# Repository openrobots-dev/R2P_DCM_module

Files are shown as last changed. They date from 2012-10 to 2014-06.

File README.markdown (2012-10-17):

MOTORBOARD MODULE
-----------------

This is a motor controller board that features an high power 24V, 20A H-bridge, current sense and quadrature encoder interface.
The MotorBoard module is supposed to work together with other smart modules, publishing data on CAN bus using a publish/subscriber QoS enabled middleware (under development).
The overall system should provide the devices and functionalities commonly used in robot prototyping, speeding up the development process and reducing the engineering time, leaving more time to research activities. The system is also supposed to enable students and amateurs to easily build robots without advanced hardware knowledge.

### Hardware

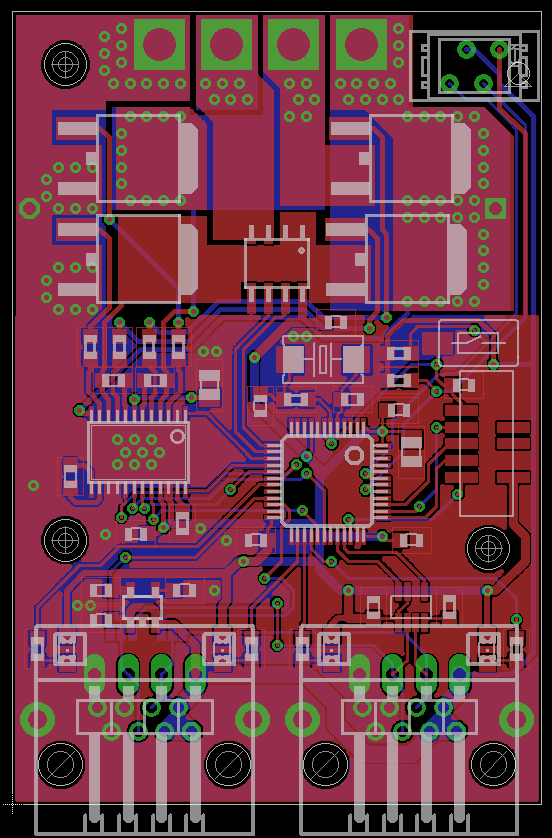
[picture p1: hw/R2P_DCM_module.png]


The MotorBoard module is run by a STM32 ARM Cortex-M3 microcontroller that generates driving signals for the H-Bridge, monitors the current drawn by the motor and reads the incremental encoder feedback.
The microcontroller also runs a PID controller that can follow a position, speed or current (torque) set-point received on a specific topic over the CAN bus network.

The power stage of the MotorBoard features:

- ST STD120N4F6 N-channel 40 V, 3.5 mOhm, 80A power MOSFETs
- Allegro A4941 MOSFET driver
- Allegro ACS711 Hall-effect current sensor

Modules are connected together by a single cable, that transports CAN signals and 5V power. Each module has two ports, enabling chain connections.

A double connector footprint (RJ45 + pin header) is provided, so the user can choose which cabling fits better his needs:

- RJ45 has been chosen as it provides shielded twisted wires for 1Mbit CAN networking in harsh environments and cables are easy to find.
- pin header has been chosen to also give a space saving and simple connection when modules are close and RJ45 jack/plug pairing space is a problem. This header also enables using the IMU module outside our framework, accessing it through a simple TTL UART interface.

The four status LEDs are placed under RJ45 plug light pipes entrance, so it is only needed to solder the preferred connector without any other layout changes.

The left connector has the option to expose the TTL UART interface, instead of the CAN bus interface, by a solder jumper placed on the bottom of the board.

### Firmware

A demo firmware which tests the various hardware components is available.
The full firmware featuring closed loop control is under development.

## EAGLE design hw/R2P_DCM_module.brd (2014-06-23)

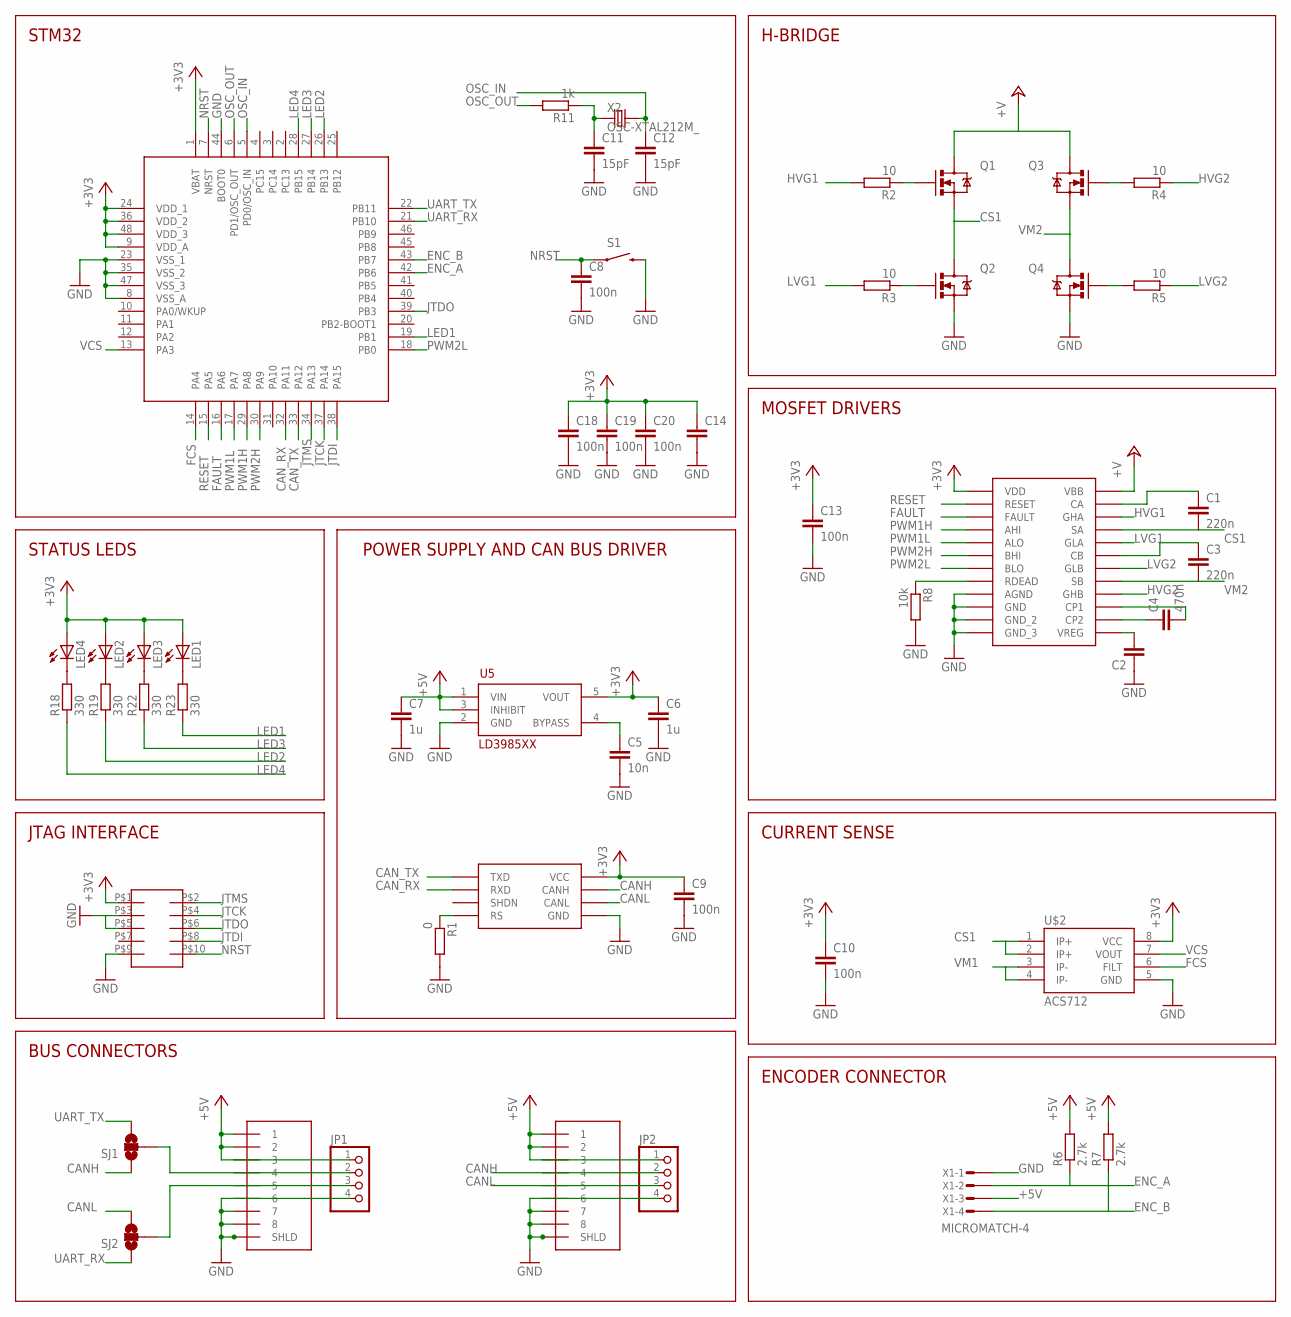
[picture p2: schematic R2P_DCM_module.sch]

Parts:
1, 2: RJ45-43860; 0438600010
C1, C3: 220n; C0603
C2, C14: C-EUC0805; C0805
C4: 470n; C0603
C5: 10n; C0603
C6, C7: 1u; C0603
C8, C9, C10, C13, C18, C19, C20: 100n; C0603
C11, C12: 15pF; C0603
JP1, JP2: PINHD-1X4/90; 1X04/90
LED1, LED2, LED3, LED4: LEDCHIPLED_0805; CHIPLED_0805
Q1, Q2, Q3, Q4: MOSFET-NCHANNELFDD8580; DPAK
R1: 0; R0603
R2, R3, R4, R5: 10; R0603
R6, R7: 2.7k; R0603
R8: 10k; R0603
R11: 1k; R0603
R18, R19, R22, R23: 330; R0603
S1: SWITCH-MOMENTARY-2-SMD-1101NE; TACTILE-SWITCH-1101NE
SJ1, SJ2: SOLDERJUMPER_2WAYPASTE1&2; SJ_3_PASTE1&2
SOT1: MAX3051; SOT23-8L
U1: STM32F103CX; LQFP48
U5: LD3985XX; SOT23-5L
U$1: A4940; TSSOP24
U$2: ACS712; SO08
U$4: FTSH-105
X1: MICROMATCH-4
X2: OSC-XTAL212M_; 4X6

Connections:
+3V3: C6.1, C9.1, C10.1, C13.1, C14.1, C18.1, C19.1, C20.1, LED1.A, LED2.A, LED3.A, LED4.A, SOT1.P$3 (VCC), U1.1 (VBAT), U1.9 (VDD_A), U1.24 (VDD_1), U1.36 (VDD_2), U1.48 (VDD_3), U5.5 (VOUT), U$1.21 (VDD), U$2.8 (VCC), U$4.P$1
+5V: 1.P$1 (1), 1.P$2 (2), 1.P$3 (3), 2.P$1 (1), 2.P$2 (2), 2.P$3 (3), C7.1, JP1.1, JP2.1, R6.2, R7.2, U5.1 (VIN), U5.3 (INHIBIT), X1.3
+V: Q1.4 (D), Q3.4 (D), U$1.12 (VBB)
CANH: 2.P$4 (4), JP2.2, SJ1.1, SOT1.P$7 (CANH)
CANL: 2.P$5 (5), JP2.3, SJ2.3, SOT1.P$6 (CANL)
CAN_RX: SOT1.P$4 (RXD), U1.32 (PA11)
CAN_TX: SOT1.P$1 (TXD), U1.33 (PA12)
CS1: C1.2, Q1.3 (S), Q2.4 (D), U$1.10 (SA), U$2.1 (IP+), U$2.2 (IP+)
ENC_A: R6.1, U1.42 (PB6), X1.2
ENC_B: R7.1, U1.43 (PB7), X1.4
FAULT: U1.16 (PA6), U$1.24 (FAULT)
FCS: U1.14 (PA4), U$2.6 (FILT)
GND: 1.P$6 (6), 1.P$7 (7), 1.P$8 (8), 1.P$9 (SHLD), 1.P$10, 2.P$6 (6), 2.P$7 (7), 2.P$8 (8), 2.P$9 (SHLD), 2.P$10, C2.1, C5.2, C6.2, C7.2, C8.2, C9.2, C10.2, C11.2, C12.2, C13.2, C14.2, C18.2, C19.2, C20.2, JP1.4, JP2.4, Q2.3 (S), Q4.3 (S), R1.2, R8.2, S1.P$2 (2), SOT1.P$2 (GND), U1.8 (VSS_A), U1.23 (VSS_1), U1.35 (VSS_2), U1.44 (BOOT0), U1.47 (VSS_3), U5.2 (GND), U$1.2 (GND), U$1.15 (GND_2), U$1.16 (GND_3), U$1.22 (AGND), U$1.PAD (GND), U$2.5 (GND), U$4.P$3, U$4.P$9, X1.1
HVG1: R2.2, U$1.9 (GHA)
HVG2: R4.1, U$1.5 (GHB)
JTCK: U1.37 (PA14), U$4.P$4
JTDI: U1.38 (PA15), U$4.P$8
JTDO: U1.39 (PB3), U$4.P$6
JTMS: U1.34 (PA13), U$4.P$2
LED1: R23.1, U1.19 (PB1)
LED2: R19.1, U1.26 (PB13)
LED3: R22.1, U1.27 (PB14)
LED4: R18.1, U1.28 (PB15)
LVG1: R3.2, U$1.11 (GLA)
LVG2: R5.1, U$1.3 (GLB)
unnamed: R1.1, SOT1.P$8 (RS)
unnamed: 1.P$4 (4), JP1.2, SJ1.2
unnamed: C5.1, U5.4 (BYPASS)
unnamed: Q1.1 (G), R2.1
unnamed: Q2.1 (G), R3.1
unnamed: Q3.1 (G), R4.2
unnamed: 1.P$5 (5), JP1.3, SJ2.2
unnamed: Q4.1 (G), R5.2
unnamed: C4.1, U$1.13 (CP2)
unnamed: C4.2, U$1.14 (CP1)
unnamed: C11.1, R11.1, X2.1 (X1)
unnamed: C2.2, U$1.7 (VREG)
unnamed: LED4.C, R18.2
unnamed: C3.1, U$1.6 (CB)
unnamed: R8.1, U$1.23 (RDEAD)
unnamed: LED2.C, R19.2
unnamed: LED3.C, R22.2
unnamed: LED1.C, R23.2
unnamed: C1.1, U$1.8 (CA)
NRST: C8.1, S1.P$1 (1), U1.7 (NRST), U$4.P$10
OSC_IN: C12.1, U1.5 (PD0/OSC_IN), X2.2 (X2)
OSC_OUT: R11.2, U1.6 (PD1/OSC_OUT)
PWM1H: U1.29 (PA8), U$1.20 (AHI)
PWM1L: U1.17 (PA7), U$1.19 (ALO)
PWM2H: U1.30 (PA9), U$1.18 (BHI)
PWM2L: U1.18 (PB0), U$1.17 (BLO)
RESET: U1.15 (PA5), U$1.1 (RESET)
UART_RX: SJ2.1, U1.21 (PB10)
UART_TX: SJ1.3, U1.22 (PB11)
VCS: U1.13 (PA3), U$2.7 (VOUT)
VM1: U$2.3 (IP-), U$2.4 (IP-)
VM2: C3.2, Q3.3 (S), Q4.4 (D), U$1.4 (SB)

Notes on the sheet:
STM32
POWER SUPPLY AND CAN BUS DRIVER
STATUS LEDS
JTAG INTERFACE
BUS CONNECTORS
H-BRIDGE
MOSFET DRIVERS
CURRENT SENSE
ENCODER CONNECTOR

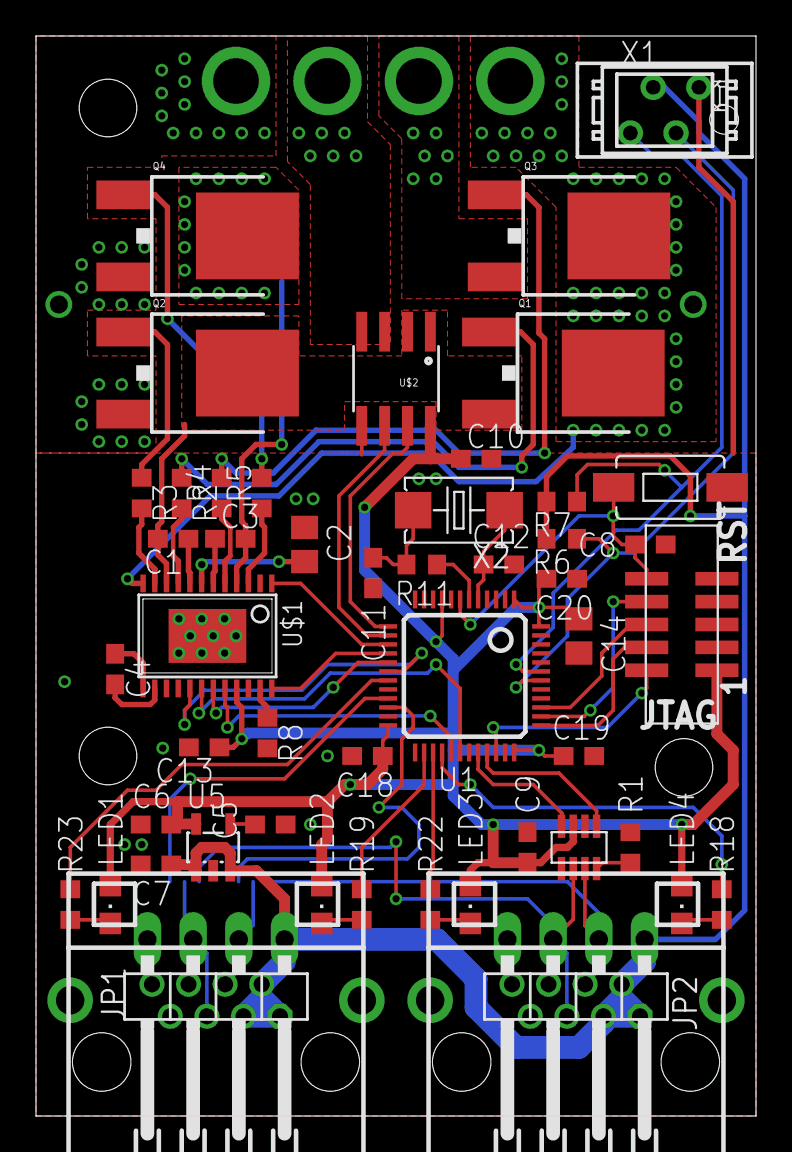
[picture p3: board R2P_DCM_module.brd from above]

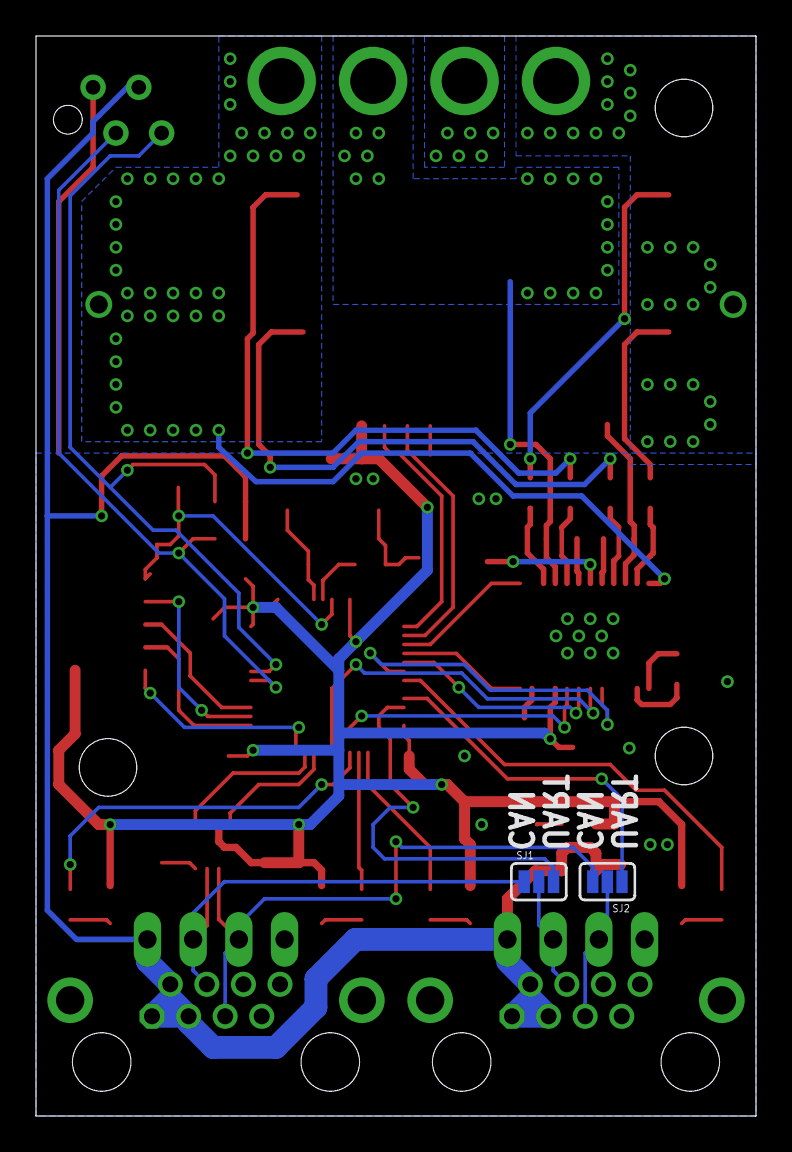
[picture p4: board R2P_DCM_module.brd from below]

Board: 2 copper layers, 40.0 x 60.0 mm, 53 parts (2 on the bottom side), 57 nets.

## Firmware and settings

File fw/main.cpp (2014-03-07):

#include "ch.h"
#include "hal.h"

#include "rtcan.h"
#include "config.h"

#include <r2p/common.hpp>
#include <r2p/Middleware.hpp>
#include <r2p/Node.hpp>
#include <r2p/Topic.hpp>
#include <r2p/Publisher.hpp>
#include <r2p/Subscriber.hpp>
#include <r2p/Mutex.hpp>
#include <r2p/NamingTraits.hpp>
#include <r2p/Bootloader.hpp>
#include "r2p/transport/RTCANTransport.hpp"

#include "r2p/node/led.hpp"

#include <cstdio>
#include <cstdlib>
#include <cstring>

#ifndef R2P_MODULE_NAME
#define R2P_MODULE_NAME "DCM"
#endif

extern "C" {
void *__dso_handle;
void __cxa_pure_virtual() {
	chSysHalt();
}
void _exit(int) {
	chSysHalt();
	for (;;) {
	}
}
int _kill(int, int) {
	chSysHalt();
	return -1;
}
int _getpid() {
	return 1;
}
} // extern "C"

static WORKING_AREA(wa_info, 2048);

r2p::Middleware r2p::Middleware::instance(R2P_MODULE_NAME,
		"BOOT_"R2P_MODULE_NAME);

// RTCAN transport
static r2p::RTCANTransport rtcantra(RTCAND1);

RTCANConfig rtcan_config = { 1000000, 100, 60 };

/*
 * Application entry point.
 */
extern "C" {
int main(void) {

	halInit();
	chSysInit();

	palClearPad(LED1_GPIO, LED1);
	palClearPad(LED2_GPIO, LED2);
	palClearPad(LED3_GPIO, LED3);
	palClearPad(LED4_GPIO, LED4);
	chThdSleepMilliseconds(500);
	palSetPad(LED1_GPIO, LED1);
	palSetPad(LED2_GPIO, LED2);
	palSetPad(LED3_GPIO, LED3);
	palSetPad(LED4_GPIO, LED4);

	r2p::Middleware::instance.initialize(wa_info, sizeof(wa_info),
			r2p::Thread::LOWEST);

	rtcantra.initialize(rtcan_config);

	r2p::Middleware::instance.start();

	r2p::Thread::create_heap(NULL, THD_WA_SIZE(512), NORMALPRIO,
			r2p::ledsub_node, NULL);

	for (;;) {
		r2p::Thread::sleep(r2p::Time::ms(500));
	}
	return CH_SUCCESS;
}
}

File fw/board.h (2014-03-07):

/*
 ChibiOS/RT - Copyright (C) 2006,2007,2008,2009,2010,
 2011 Giovanni Di Sirio.

 This file is part of ChibiOS/RT.

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
 You should have received a copy of the GNU General Public License
 along with this program.  If not, see <http://www.gnu.org/licenses/>.
 */

#ifndef _BOARD_H_
#define _BOARD_H_

/*
 * Setup for the R2P DC motor module.
 */

/*
 * Board identifier.
 */
#define BOARD_R2P_DCM_MODULE
#define BOARD_NAME              "R2P DC motor module"

/*
 * Board frequencies.
 */
#define STM32_LSECLK            32768
#define STM32_HSECLK            8000000

/*
 * MCU type, supported types are defined in ./os/hal/platforms/hal_lld.h.
 */
#define STM32F10X_MD

/*
 * IO pins assignments.
 */
#define LED1_GPIO				GPIOB
#define LED1					1
#define LED2_GPIO				GPIOB
#define LED2					13
#define LED3_GPIO				GPIOB
#define LED3					14
#define LED4_GPIO				GPIOB
#define LED4					15

#define DRIVER_GPIO             GPIOA
#define DRIVER_RESET            5
#define DRIVER_FAULT            6

#define SERIAL_DRIVER           SD3
//#define SERIAL_DRIVER           SD1

#define PWM_DRIVER              PWMD1
#define QEI_DRIVER              QEID4

/*
 * I/O ports initial setup, this configuration is established soon after reset
 * in the initialization code.
 *
 * The digits have the following meaning:
 *   0 - Analog input.
 *   1 - Push Pull output 10MHz.
 *   2 - Push Pull output 2MHz.
 *   3 - Push Pull output 50MHz.
 *   4 - Digital input.
 *   5 - Open Drain output 10MHz.
 *   6 - Open Drain output 2MHz.
 *   7 - Open Drain output 50MHz.
 *   8 - Digital input with PullUp or PullDown resistor depending on ODR.
 *   9 - Alternate Push Pull output 10MHz.
 *   A - Alternate Push Pull output 2MHz.
 *   B - Alternate Push Pull output 50MHz.
 *   C - Reserved.
 *   D - Alternate Open Drain output 10MHz.
 *   E - Alternate Open Drain output 2MHz.
 *   F - Alternate Open Drain output 50MHz.
 * Please refer to the STM32 Reference Manual for details.
 */

/*
 * Port A setup.
 * Everything input with pull-up except:
 * PA3  - Analog input     (CS_OUT).
 * PA4  - Input with PU    (CS_FAULT).
 * PA5  - Push Pull output (DRIVER_RESET).
 * PA6  - Input with PU    (DRIVER_FAULT).
 * PA7  - Alternate output (PWM1L).
 * PA8  - Alternate output (PWM1H).
 * PA9  - Alternate output (PWM2H).
 * PA11 - Normal input     (CAN1 RX).
 * PA12 - Alternate output (CAN1 TX).
 */
#define VAL_GPIOACRL            0xB8380888      /*  PA7...PA0 */
#define VAL_GPIOACRH            0x888B48BB      /* PA15...PA8 */
#define VAL_GPIOAODR            0xFFFFFFFF

/*
 * Port B setup.
 * Everything input with pull-up except:
 *
 * PB0  - Alternate output (PWM2L).
 * PB1  - Push Pull output (LED1).
 * PB6  - Normal input (ENC_A).
 * PB7  - Normal input (ENC_B).
 * PB10 - Alternate output (USART3 TX).
 * PB11 - Normal input     (USART3 RX).
 * PB13 - Push Pull output (LED2).
 * PB14 - Push Pull output (LED3).
 * PB15 - Push Pull output (LED4).
 */
#define VAL_GPIOBCRL            0x4488883B      /*  PB7...PB0 */
//#define VAL_GPIOBCRL            0x4B88883B      /*  XXX USART1 REMAP */
#define VAL_GPIOBCRH            0x33384BFF      /* PB15...PB8 */
#define VAL_GPIOBODR            0xFFFFFFFF

/*
 * Port C setup.
 * Everything input with pull-up except:
 */
#define VAL_GPIOCCRL            0x88888888      /*  PC7...PC0 */
#define VAL_GPIOCCRH            0x88888888      /* PC15...PC8 */
#define VAL_GPIOCODR            0xFFFFFFFF

#if !defined(_FROM_ASM_)
#ifdef __cplusplus
extern "C" {
#endif
void boardInit(void);
#ifdef __cplusplus
}
#endif
#endif /* _FROM_ASM_ */

#endif /* _BOARD_H_ */

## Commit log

2012-07-24 Removed signals under A4940
    [MotorBoard.brd, MotorBoard.sch]
2012-07-24 Typo in schematics and board layout filename
    [R2P_DCM_v2.brd, R2P_DCM_v2.sch]
2012-07-24 Powerpad under A4940
    [R2P_DCM_v2.brd]
2012-07-30 Datasheets added
    [R2P_DCM_v2.brd, R2P_DCM_v2.sch]
2012-07-30 .gitignore added to revision control
    [R2P_DCM_module.brd, R2P_DCM_module.sch]
2012-08-28 Update MCU layout
    [R2P_DCM_module.brd, R2P_DCM_module.sch]
2012-10-16 Added encoder interface
2012-10-17 Added board .png
2012-10-17 Updated board.png
2012-11-22 Removed misplaced via and disconnected MAX3051 shutdown pin
    [R2P_DCM_module.brd, R2P_DCM_module.sch]
2013-08-01 increased bootstrap capacitor value
    [R2P_DCM_module.brd, R2P_DCM_module.sch]
2013-08-01 Corrected RDEAD value
    [R2P_DCM_module.brd, R2P_DCM_module.sch]
2014-03-07 updated sample firmware to mw v2
2014-06-23 removed duplicated via
    [R2P_DCM_module.brd]
